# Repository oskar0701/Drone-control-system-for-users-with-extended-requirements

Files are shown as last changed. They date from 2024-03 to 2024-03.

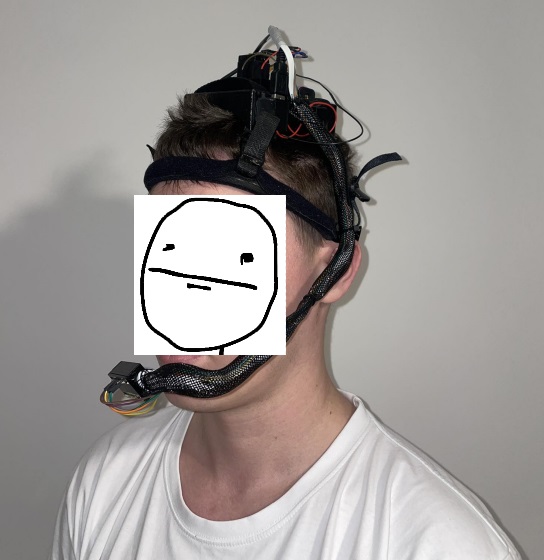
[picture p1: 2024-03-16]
project.jpg

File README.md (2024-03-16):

# Drone-control-system-using-gyro-and-micro-speech-model
The hands-free control system for the DJI Tello drone.

The project involves creating a head-mounted platform that allows controlling the flight of a DJI Tello drone using gyroscope readings and recognized voice commands using a model trained on the Tensorflow Lite engine.

To create the project, please assemble the following components:
  - MPU6050 3-axis gyro module,
  - ESP32,
  - Arduino Nano 33 BLE Sense (The rev2 version was used, but the basic version can also be utilized),
  - On/off switch like e.g SMRS-1,
  - 18650 battery and charging module with 5V step-up converter,
  - couple of wires,
  - DJI Tello drone.
  - 3D printer (optional)

****CONNECTION DIAGRAM****

Connect the elements according to the following diagram. You can power the microcontrollers via the USB port or directly to the pins, but remember that Arduino Nano Sense cannot be powered with 5V directly to the pins. If you want to power this board using the pins, you must first connect the jumper at the bottom of the board. The connected GPIO pins between the two boards are responsible for 6 voice commands, the recognition of which is signaled by a high state.
The commands available in the project are: up, down, left, right, forward and backward.

schemat

To embed electronic components, you can use the 3D printed control platform project. The files are located in the prints folder.

**ESP SIDE**

It's best to start by uploading the program to the control side of the drone, i.e., the ESP32. The program also includes sending flight instructions based on gyroscope axis deflections and handling voice commands coming from another microcontroller, but more on that in a moment.

The changes you need to make in the code involve declaring the SSID broadcasted by your drone and the password. If you don't know the password, you probably never changed it - by default, it's empty. 



If you wish, you can make changes to the threshold values in ifology(:D) for axis deflections for your convenience of use.

Flash the code to the board. Now you can control the flight of the drone using the gyroscope connected to the board. The startup procedure is automatic as soon as the connection with the drone is established. However, remember that at this stage, the code does not include landing (unless you set a high state on the pin corresponding to the 'down' command).

**ARDUINO SIDE**

Flash the code to the board using Arduino mbedOS package that you can find in your board manager. The code provides for the recognition of 6 voice commands, the recognition of which causes a high state on the appropriate pin. 

If you want to train your own model, read this article: https://www.hackster.io/shahizat/micro-speech-command-recognition-with-tensorflow-lite-44dc5a

Check whether command recognition does not enter the noise band by manipulating the value of the detection_threshold variable in the recognize commands.h header file. In my case, setting the value of this variable to 160 gave the best results.



**SOFTWARE INTEGRATION**

The boards communicate using logical 0 and 1. When a voice command is recognized, the high state is displayed for a second. During this time, it is received by ESP32 and, depending on the pin, the drone's flight instructions are handled. 

Functionalities available for each command:
- up: increasing the height by 50cm,
- down: decreasing the height by 40cm or landing if the drone is at a height below 30 cm,
- left: ccw 40 degress,
- right: cw 40 degress,
- forward: frontflip,
- backward: backflip,

If you want, you can declare your own command support.

The project's operation is presented in the following network of activities:

Diagram bez tytułu (1)

**BIBLIOGRAPHY**

Tello control lib: https://github.com/akshayvernekar/telloArduino

Tensorflow Lite examples: https://www.tensorflow.org/lite/microcontrollers

Mouting tray for MPU6050: https://www.thingiverse.com/thing:4912985

Powerbank module 134n3P / 1S 18650: https://www.thingiverse.com/thing:3867064

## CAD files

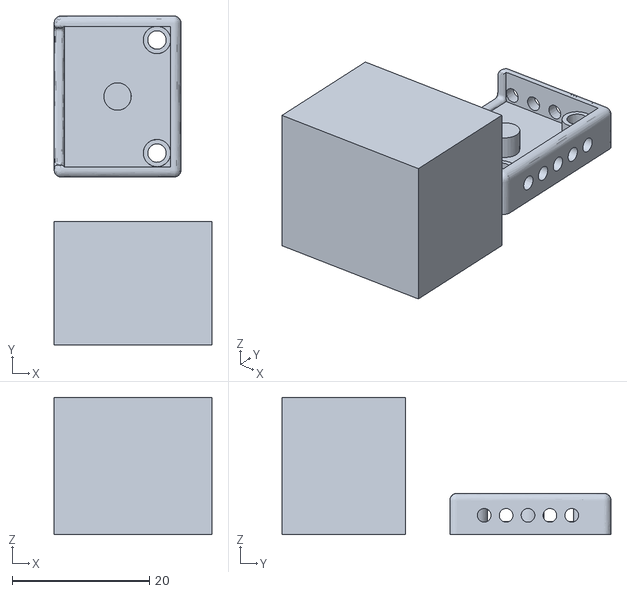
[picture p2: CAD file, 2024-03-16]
prints/Base and housing for MPU6050.stl
23.0 x 48.0 x 20.0

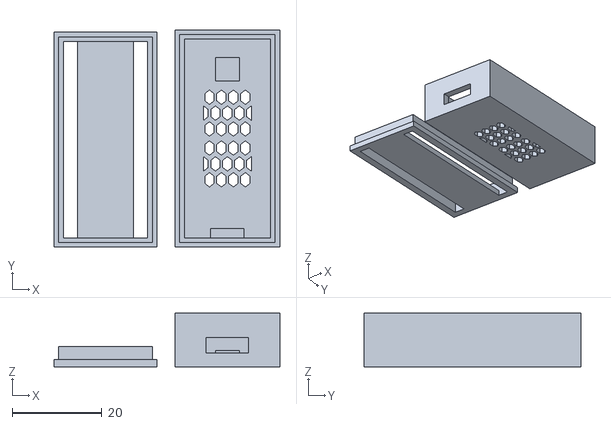
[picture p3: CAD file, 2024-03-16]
prints/Arduino housing.stl
50.5 x 48.5 x 12.0

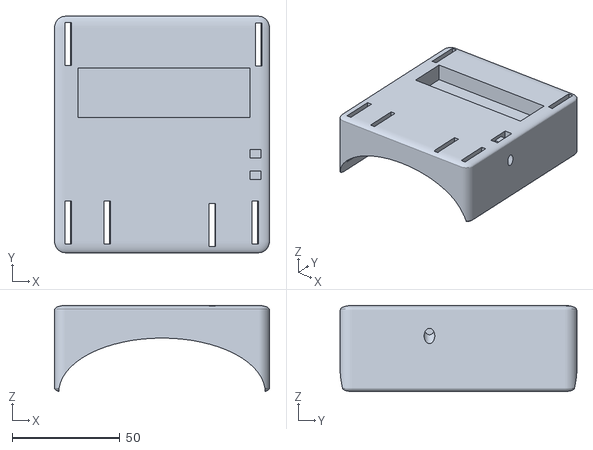
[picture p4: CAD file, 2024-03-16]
prints/Control platform.stl
100.0 x 110.0 x 40.0

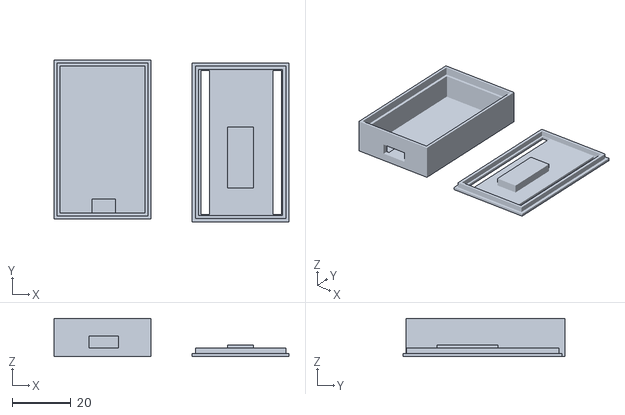
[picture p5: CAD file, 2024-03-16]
prints/ESP32 housing.stl
80.0 x 55.0 x 13.0

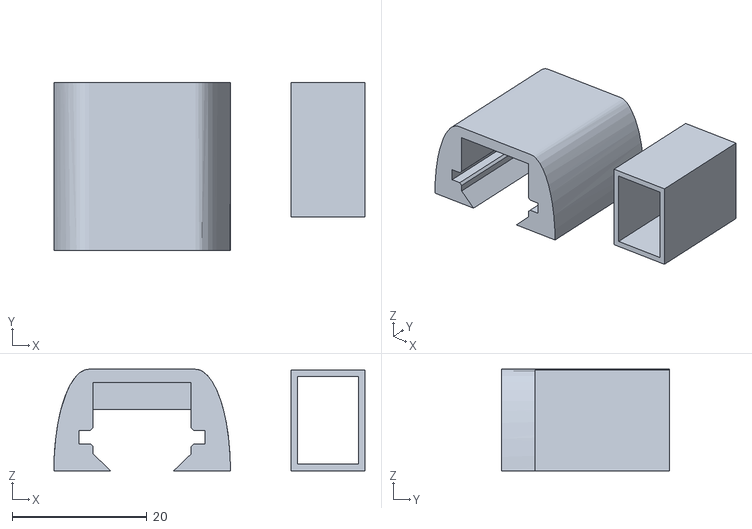
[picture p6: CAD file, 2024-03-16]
prints/134n3p & SMRS-1.stl
46.2 x 25.0 x 15.1

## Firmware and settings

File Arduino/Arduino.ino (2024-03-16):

/* Copyright 2023 The TensorFlow Authors. All Rights Reserved.

  Licensed under the Apache License, Version 2.0 (the "License");
  you may not use this file except in compliance with the License.
  You may obtain a copy of the License at

    http://www.apache.org/licenses/LICENSE-2.0

  Unless required by applicable law or agreed to in writing, software
  distributed under the License is distributed on an "AS IS" BASIS,
  WITHOUT WARRANTIES OR CONDITIONS OF ANY KIND, either express or implied.
  See the License for the specific language governing permissions and
  limitations under the License.
  ==============================================================================*/

#include <TensorFlowLite.h>

#include "audio_provider.h"
#include "command_responder.h"
#include "feature_provider.h"
#include "main_functions.h"
#include "micro_features_micro_model_settings.h"
#include "micro_features_model.h"
#include "recognize_commands.h"
#include "tensorflow/lite/micro/micro_interpreter.h"
#include "tensorflow/lite/micro/micro_log.h"
#include "tensorflow/lite/micro/micro_mutable_op_resolver.h"
#include "tensorflow/lite/micro/system_setup.h"
#include "tensorflow/lite/schema/schema_generated.h"

#undef PROFILE_MICRO_SPEECH

// Globals, used for compatibility with Arduino-style sketches.
namespace {
const tflite::Model* model = nullptr;
tflite::MicroInterpreter* interpreter = nullptr;
TfLiteTensor* model_input = nullptr;
FeatureProvider* feature_provider = nullptr;
RecognizeCommands* recognizer = nullptr;
int32_t previous_time = 0;

// Create an area of memory to use for input, output, and intermediate arrays.
// The size of this will depend on the model you're using, and may need to be
// determined by experimentation.
constexpr int kTensorArenaSize = 10 * 1024;
// Keep aligned to 16 bytes for CMSIS
alignas(16) uint8_t tensor_arena[kTensorArenaSize];
int8_t feature_buffer[kFeatureElementCount];
int8_t* model_input_buffer = nullptr;
}  // namespace

// The name of this function is important for Arduino compatibility.
void setup() {
  tflite::InitializeTarget();

  // Map the model into a usable data structure. This doesn't involve any
  // copying or parsing, it's a very lightweight operation.
  model = tflite::GetModel(g_model);
  if (model->version() != TFLITE_SCHEMA_VERSION) {
    MicroPrintf(
      "Model provided is schema version %d not equal "
      "to supported version %d.",
      model->version(), TFLITE_SCHEMA_VERSION);
    return;
  }

  // Pull in only the operation implementations we need.
  // This relies on a complete list of all the ops needed by this graph.
  // An easier approach is to just use the AllOpsResolver, but this will
  // incur some penalty in code space for op implementations that are not
  // needed by this graph.
  //
  // tflite::AllOpsResolver resolver;
  // NOLINTNEXTLINE(runtime-global-variables)
  static tflite::MicroMutableOpResolver<5> micro_op_resolver;
  if (micro_op_resolver.AddConv2D() != kTfLiteOk) {
    return;
  }
  if (micro_op_resolver.AddDepthwiseConv2D() != kTfLiteOk) {
    return;
  }
  if (micro_op_resolver.AddFullyConnected() != kTfLiteOk) {
    return;
  }
  if (micro_op_resolver.AddSoftmax() != kTfLiteOk) {
    return;
  }
  if (micro_op_resolver.AddReshape() != kTfLiteOk) {
    return;
  }

  // Build an interpreter to run the model with.
  static tflite::MicroInterpreter static_interpreter(
    model, micro_op_resolver, tensor_arena, kTensorArenaSize);
  interpreter = &static_interpreter;

  // Allocate memory from the tensor_arena for the model's tensors.
  TfLiteStatus allocate_status = interpreter->AllocateTensors();
  if (allocate_status != kTfLiteOk) {
    MicroPrintf("AllocateTensors() failed");
    return;
  }

  // Get information about the memory area to use for the model's input.
  model_input = interpreter->input(0);
  if ((model_input->dims->size != 2) || (model_input->dims->data[0] != 1) ||
      (model_input->dims->data[1] !=
       (kFeatureSliceCount * kFeatureSliceSize)) ||
      (model_input->type != kTfLiteInt8)) {
    MicroPrintf("Bad input tensor parameters in model");
    return;
  }
  model_input_buffer = model_input->data.int8;

  // Prepare to access the audio spectrograms from a microphone or other source
  // that will provide the inputs to the neural network.
  // NOLINTNEXTLINE(runtime-global-variables)
  static FeatureProvider static_feature_provider(kFeatureElementCount,
      feature_buffer);
  feature_provider = &static_feature_provider;

  static RecognizeCommands static_recognizer;
  recognizer = &static_recognizer;

  previous_time = 0;

  // start the audio
  TfLiteStatus init_status = InitAudioRecording();
  if (init_status != kTfLiteOk) {
    MicroPrintf("Unable to initialize audio");
    return;
  }

  MicroPrintf("Initialization complete");
}

// The name of this function is important for Arduino compatibility.
void loop() {
#ifdef PROFILE_MICRO_SPEECH
  const uint32_t prof_start = millis();
  static uint32_t prof_count = 0;
  static uint32_t prof_sum = 0;
  static uint32_t prof_min = std::numeric_limits<uint32_t>::max();
  static uint32_t prof_max = 0;
#endif  // PROFILE_MICRO_SPEECH

  // Fetch the spectrogram for the current time.
  const int32_t current_time = LatestAudioTimestamp();
  int how_many_new_slices = 0;
  TfLiteStatus feature_status = feature_provider->PopulateFeatureData(
                                  previous_time, current_time, &how_many_new_slices);
  if (feature_status != kTfLiteOk) {
    MicroPrintf("Feature generation failed");
    return;
  }
  previous_time += how_many_new_slices * kFeatureSliceStrideMs;
  // If no new audio samples have been received since last time, don't bother
  // running the network model.
  if (how_many_new_slices == 0) {
    return;
  }

  // Copy feature buffer to input tensor
  for (int i = 0; i < kFeatureElementCount; i++) {
    model_input_buffer[i] = feature_buffer[i];
  }

  // Run the model on the spectrogram input and make sure it succeeds.
  TfLiteStatus invoke_status = interpreter->Invoke();
  if (invoke_status != kTfLiteOk) {
    MicroPrintf("Invoke failed");
    return;
  }

  // Obtain a pointer to the output tensor
  TfLiteTensor* output = interpreter->output(0);
  // Determine whether a command was recognized based on the output of inference
  const char* found_command = nullptr;
  uint8_t score = 0;
  bool is_new_command = false;
  TfLiteStatus process_status = recognizer->ProcessLatestResults(
                                  output, current_time, &found_command, &score, &is_new_command);
  if (process_status != kTfLiteOk) {
    MicroPrintf("RecognizeCommands::ProcessLatestResults() failed");
    return;
  }
  // Do something based on the recognized command. The default implementation
  // just prints to the error console, but you should replace this with your
  // own function for a real application.
  RespondToCommand(current_time, found_command, score, is_new_command);

#ifdef PROFILE_MICRO_SPEECH
  const uint32_t prof_end = millis();
  if (++prof_count > 10) {
    uint32_t elapsed = prof_end - prof_start;
    prof_sum += elapsed;
    if (elapsed < prof_min) {
      prof_min = elapsed;
    }
    if (elapsed > prof_max) {
      prof_max = elapsed;
    }
    if (prof_count % 300 == 0) {
      MicroPrintf("## time: min %dms  max %dms  avg %dms", prof_min, prof_max,
                  prof_sum / prof_count);
    }
  }
#endif  // PROFILE_MICRO_SPEECH
}

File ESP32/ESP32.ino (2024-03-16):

#include <Tello.h>

#include <Tello.h>
#include "MPU6050.h"      //libs importing
#include "Wire.h"
#include "I2Cdev.h"

MPU6050 mpu;              //creating mpu object of the MPU6050 class
int16_t ax, ay, az;       //gyro axis variable declarations
int16_t gx, gy, gz;

struct MyData {
  byte X;                 //creating a structure storing the X and Y fields
  byte Y;
};

MyData data;              //creating a data object of the MyData data type

// SSID and password:
const char * networkName = "TELLO-??????";
const char * networkPswd = "";
boolean connected = false;

Tello tello;              //creating tello object

const int up = 27;
const int down = 4;
const int left = 5;       //pin numbering of voice commands
const int right = 18; 
const int fwd = 17;
const int backward = 16;

void setup()
{
  Serial.begin(115200);     //opening the serial port

  pinMode(up, INPUT_PULLDOWN);
  pinMode(down, INPUT_PULLDOWN);
  pinMode(left, INPUT_PULLDOWN);      //pin setting as input, with pull-down resistor
  pinMode(right, INPUT_PULLDOWN);
  pinMode(fwd, INPUT_PULLDOWN);
  pinMode(backward, INPUT_PULLDOWN);

  Wire.begin();
  mpu.initialize();                   //I2C bus configuration
  connectToWiFi(networkName, networkPswd);
}

void loop()
{
  if (connected) {
    mpu.getMotion6(&ax, &ay, &az, &gx, &gy, &gz);
    data.X = map(ax, -17000, 17000, 0, 100); //mapping X axis values
    data.Y = map(ay, -17000, 17000, 0, 100); //mapping Y axis values

    delay(10);

    int upstate = digitalRead(up);
    int downstate = digitalRead(down);
    int leftstate = digitalRead(left);        //pin states readings
    int rightstate = digitalRead(right);
    int forwardstate = digitalRead(fwd);
    int backwardstate = digitalRead(backward);

    int height = tello.getHeight();         //current height saved to a variable
    delay(10);

    if (upstate == 1) {
      tello.sendRCcontrol(0, 0, 50, 0);     //increasing flight altitude - up command
      delay(1000);
    }

    if (downstate == 1 and height < 3) {
      tello.land();                        //landing - command down, below 3dm
      delay(5000);
    }

    if (downstate == 1 and height > 2) {
      tello.sendRCcontrol(0, 0, -40, 0);  //flight descent - command down, above 2 dm
      delay(2000);
    }

    if (leftstate == 1) {
      tello.sendRCcontrol(0, 0, 0, -40);    //cw
      delay(500);

    }

    if (rightstate == 1) {
      tello.sendRCcontrol(0, 0, 0, 40);     //ccw
      delay(500);
    }

    if (forwardstate == 1) {
      delay(100);
      tello.flip_front();                 //frontflip
      delay(500);
    }

    if (backwardstate == 1) {
      delay(100);
      tello.flip_back();                  //abackflip
      delay(500);
    }

    if (data.Y < 35) {
      tello.sendRCcontrol(-70, 0, 0, 0);    //fly left
      delay(100);
    }

    if (data.Y > 65) {
      tello.sendRCcontrol(70, 0, 0, 0);     //fly right
      delay(100);
    }

    if (data.X > 55) {
      tello.sendRCcontrol(0, -70, 0, 0);     //fly backward
      delay(100);
    }

    if (data.X < 35) {
      tello.sendRCcontrol(0, 70, 0, 0);      //fly forward
      delay(100);
    }

    if (data.X > 40 and data.X < 50 and data.Y < 60 and data.Y > 40) {
      tello.sendRCcontrol(0, 0, 0, 0);        //hold the position
      delay(100);
    }
  }
}

void connectToWiFi(const char * ssid, const char * pwd)
{
  Serial.println("Connecting to WiFi network " + String(ssid));
  WiFi.disconnect(true);
  WiFi.onEvent(WiFiEvent);
  WiFi.begin(ssid, pwd);
  Serial.println("Waiting for connection...");
}

void WiFiEvent(WiFiEvent_t event)
{
  switch (event)
  {
    case SYSTEM_EVENT_STA_GOT_IP:
      Serial.print("WiFi connected! IP address: ");
      Serial.println(WiFi.localIP());
      tello.init();
      delay(500);
      connected = true;
      tello.takeoff();        //takeoff procedure when an IP address is obtained
      delay(2000);
      break;

    case SYSTEM_EVENT_STA_DISCONNECTED:
      Serial.println("WiFi lost connection");     //connection lost
      connected = false;
      break;
  }
}
